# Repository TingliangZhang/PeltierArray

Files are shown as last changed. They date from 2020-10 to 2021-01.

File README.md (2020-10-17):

# PeltierArray
帕尔贴阵列 PCB and design

## 选型

MCU: Mega 2560 PRO (Embed) CH340G/ATmega2560-16AU

https://robotdyn.com/mega-2560-pro-embed-ch340g-atmega2560-16au.html

MOS管

[MOS(场效应管)/KIA50N03BD](https://item.szlcsc.com/458575.html)

接口

JST丨常用系列和型号选型推荐大全

https://www.szlcsc.com/info/13106.html

> 一开始选择 **PH系列 插座 1\*4P 间距2mm 卧插** B4B-PH-SM4-TB(LF)
>

后更改方案为

帕尔贴接口为PH2.0x2

PH-2A 2P 脚距2.0mm 直插

https://item.szlcsc.com/2693.html

温度传感器接口保持原来的

XH插座 1*2P 直针 间距2.5mm

https://item.szlcsc.com/169360.html

电源接口

> DC头：**DC连接器 DC-002-2.0A-1.3 DC插座 W11.4XD5.0XH7.4,内芯1.3,2A 12V**
>
> https://item.szlcsc.com/353351.html
>
> 可能要稍稍掰弯

更改为[AC/DC电源插座/DC-005 5.5-2.0MM 铁材质](https://item.szlcsc.com/16896.html)

发光二极管

LED灯绿_Iv=112-285_λd=520-535 二极管_发光二极管

SMT

或手贴

翠绿LED

https://item.szlcsc.com/207066.html

电容

[贴片电容/47uF(476) ±20% 25V](https://item.szlcsc.com/389810.html)

[引线型铝电解电容/47uF 50V黑高频](https://item.szlcsc.com/46672.html)

[贴片电容/10uF(106) ±20% 25V](https://item.szlcsc.com/97651.html)

其他

[肖特基二极管/SS14](https://item.szlcsc.com/2857.html)

[发光二极管/翠绿LED](https://item.szlcsc.com/207066.html)

半桥驱动

参考 [**wavgat**](https://wavgat.tmall.com/) 的MOS管驱动模块

https://detail.tmall.com/item.htm?id=599634712152

他上面用的MOS是[AOD4184A](https://item.szlcsc.com/100337.html)，N沟道

暂定选用[KIA50N03BD](https://item.szlcsc.com/458575.html)

封装为TO-252-2

## 3D MODEL

`.3dshapes`文件夹里面放`.step`和 `.wrl`模型文件，再在PCBNEW里面的元件封装属性里面选3D Setting添加3D Model，调整偏移对齐即可。

## Duplicate PCB sch and layout

参考

https://forum.kicad.info/t/how-to-duplicate-a-pcb-layout-in-kicad-5/12909

https://forum.kicad.info/t/replicate-layout-action-plugin/8539

https://github.com/MitjaNemec/Kicad_action_plugins

前提Hierarchical schematics：

https://docs.kicad-pcb.org/5.1/en/eeschema/eeschema.html#hierarchical-schematics

## 改为正反均要后需要用全桥

A5988:四路 DMOS 全桥式 PWM 电机驱动器

https://www.allegromicro.com/zh-CN/Products/Motor-Drivers/Brush-DC-Motor-Drivers/A5988

或者TB6612

https://toshiba.semicon-storage.com/us/semiconductor/product/motor-driver-ics/brushed-dc-motor-driver-ics/detail.TB6612FNG.html

或者DRV8833

https://www.ti.com/product/DRV8833

或者用以上两款电机驱动的Breakout Board，方便坏了的话更换。

或者参考Adafruit TB6612 1.2A DC/Stepper Motor Driver Breakout Board设计自己画

https://www.adafruit.com/product/2448

## 排针排母

TB6612 1x8排母

Mega Pro 2x3排母+2x16排母+2x21排母

只买2x20 2x3排母，剪一下

## TD1509配套电路

总体按照8V ~ 18V输入 5V 输出设计

SS52F肖特基二极管 20V 5A

https://item.szlcsc.com/328975.html

33uH 4.5A功率电感

https://item.szlcsc.com/160864.html

更便宜的选择：5A的33uH

https://item.szlcsc.com/338378.html

330uf/25V过孔电容

https://item.szlcsc.com/2403.html

## V2焊接过程中发现的问题

电感封装不对

TB6612引脚错误

没有开关（买个带开关的开关电源或者加一个12V回路功率开关）

指示灯，5V加LED+10k

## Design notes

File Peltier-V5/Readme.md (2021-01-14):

# 大板子设计

[PCA9685PW](https://www.nxp.com/part/PCA9685PW#/)

[AIP74HC4051](https://lcsc.com/product-detail/74-Series_Wuxi-I-core-Elec-AIP74HC4051_C93010.html)

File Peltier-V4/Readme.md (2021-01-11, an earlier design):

# 模块化帕尔贴设计

[BTN8982TA](https://www.infineon.com/cms/en/product/power/motor-control-ics/brushed-dc-motor-driver-ics/single-half-bridge-ics/btn8982ta/)

[6N137](https://toshiba.semicon-storage.com/ap-en/semiconductor/product/optoelectronics/detail.6N137.html)

[OPA2374](https://www.ti.com/product/OPA2374)

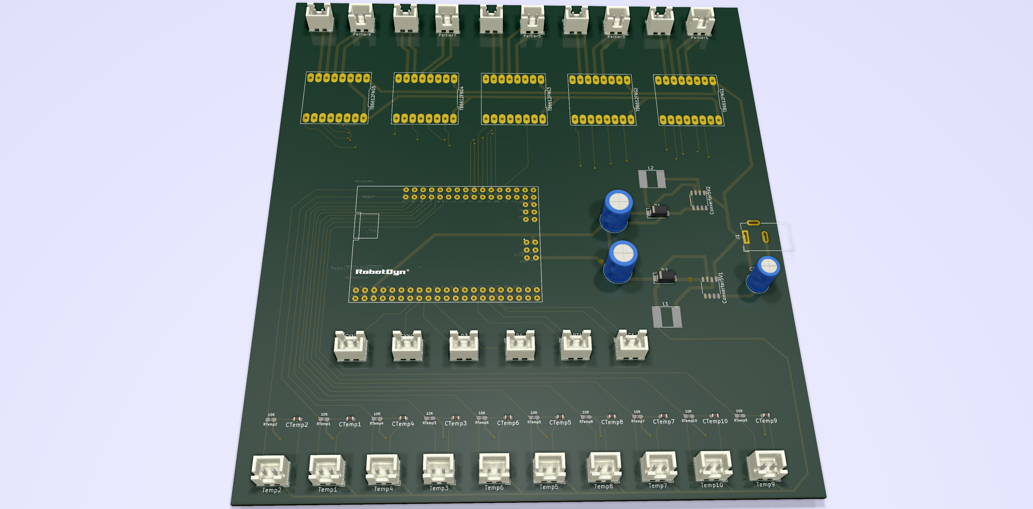
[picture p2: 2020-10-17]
Screenshot/屏幕截图 2020-10-17 140903.png

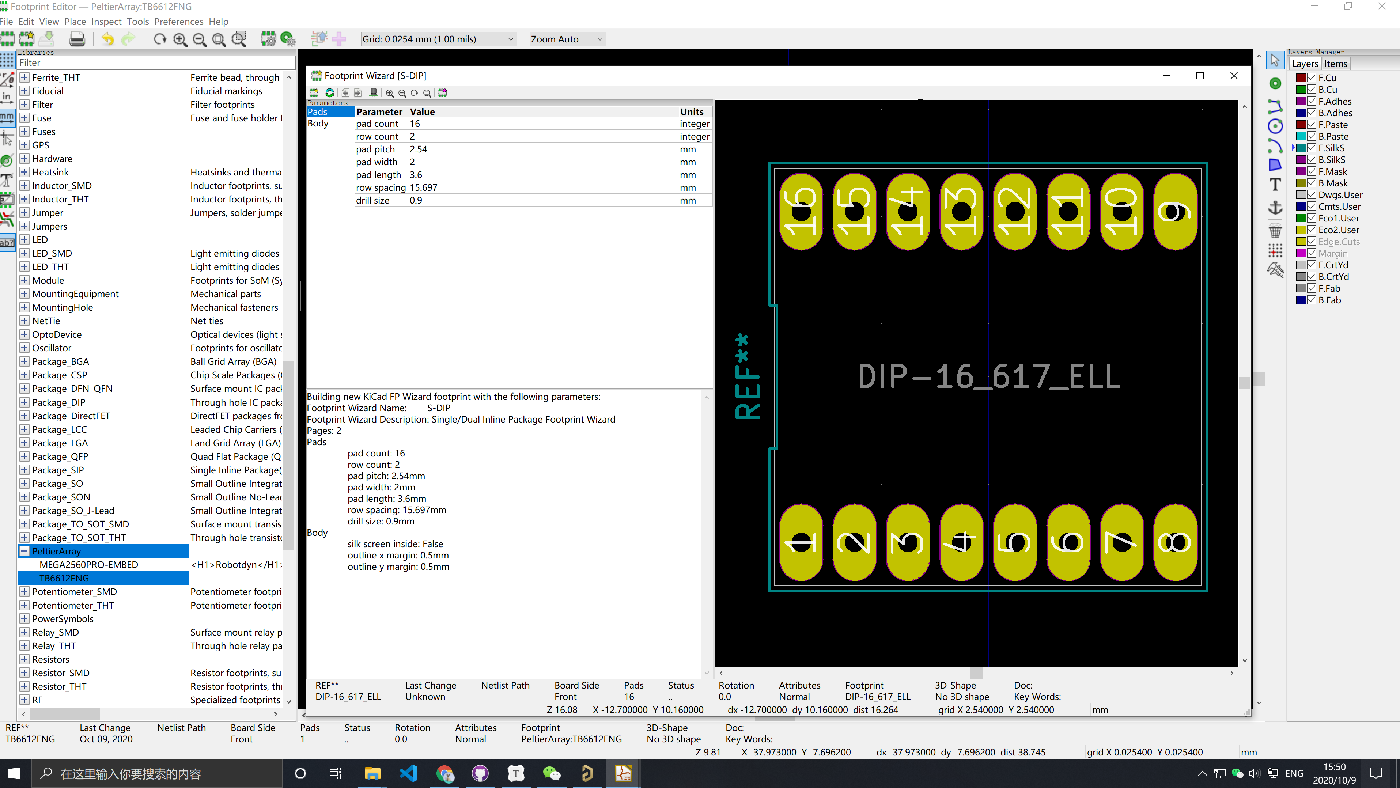
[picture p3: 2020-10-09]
Screenshot/屏幕截图 2020-10-09 155059.png

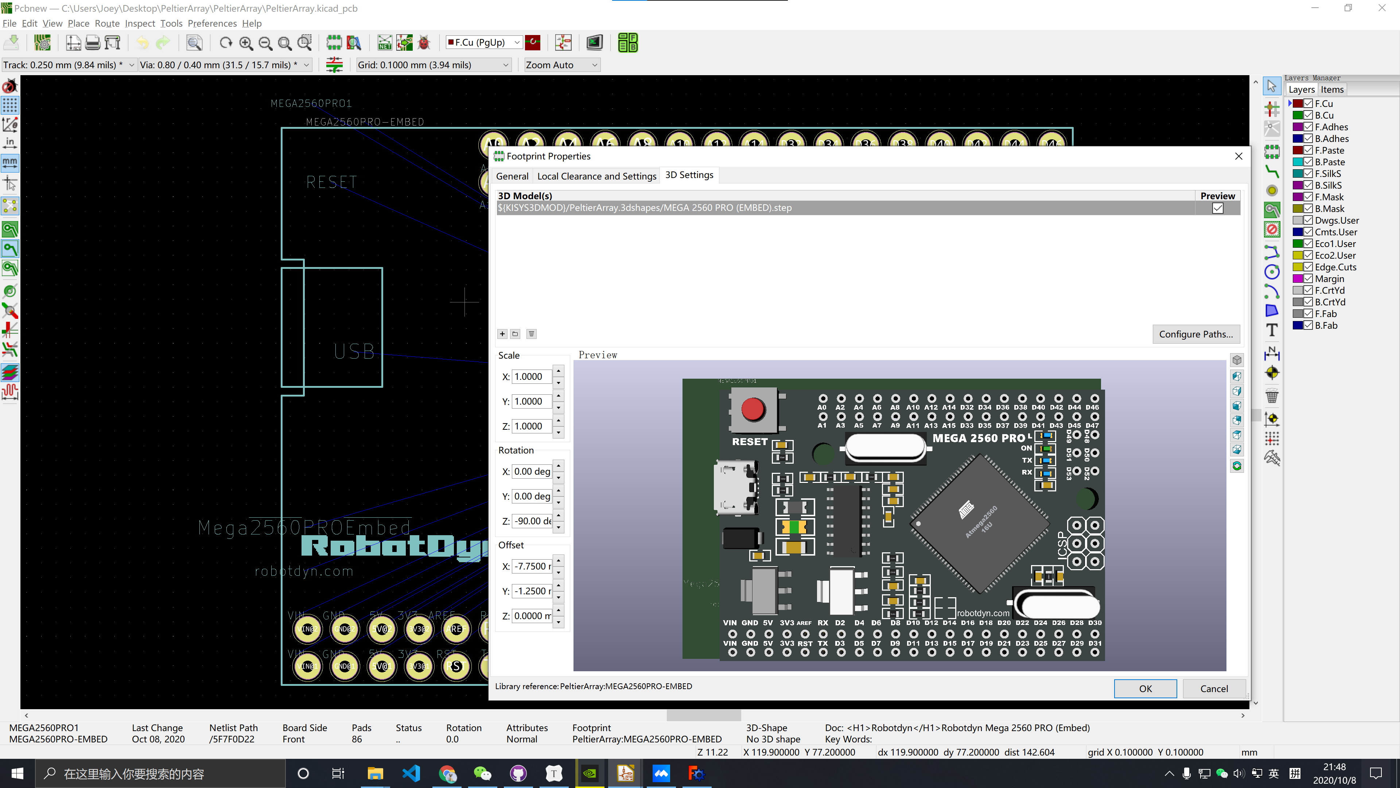
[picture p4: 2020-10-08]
ScreenShot/屏幕截图 2020-10-08 214903.png

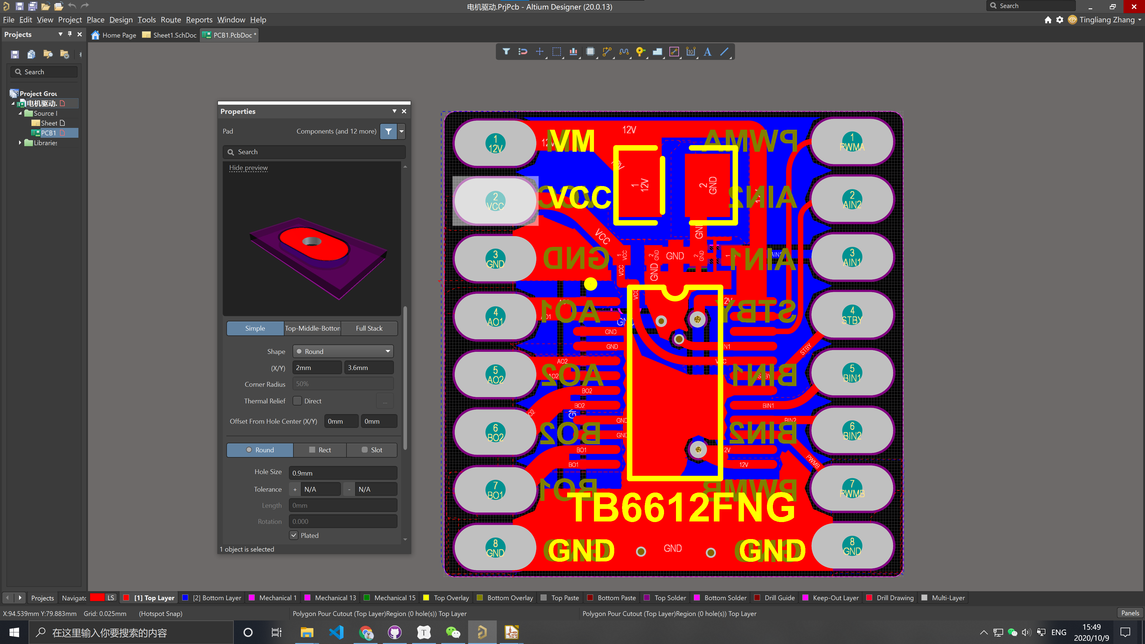
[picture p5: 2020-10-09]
Screenshot/屏幕截图 2020-10-09 154931.png

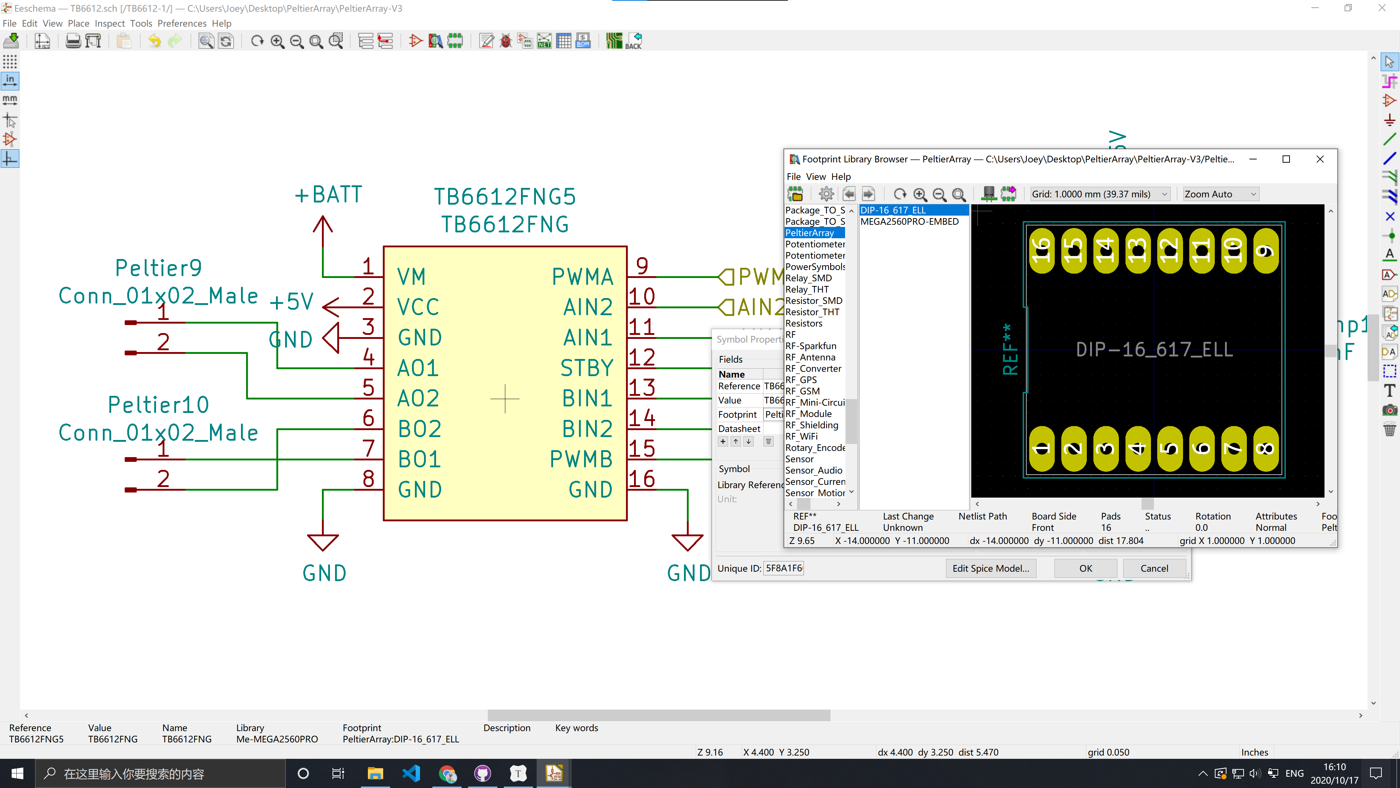
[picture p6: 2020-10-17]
Screenshot/屏幕截图 2020-10-17 161026.png

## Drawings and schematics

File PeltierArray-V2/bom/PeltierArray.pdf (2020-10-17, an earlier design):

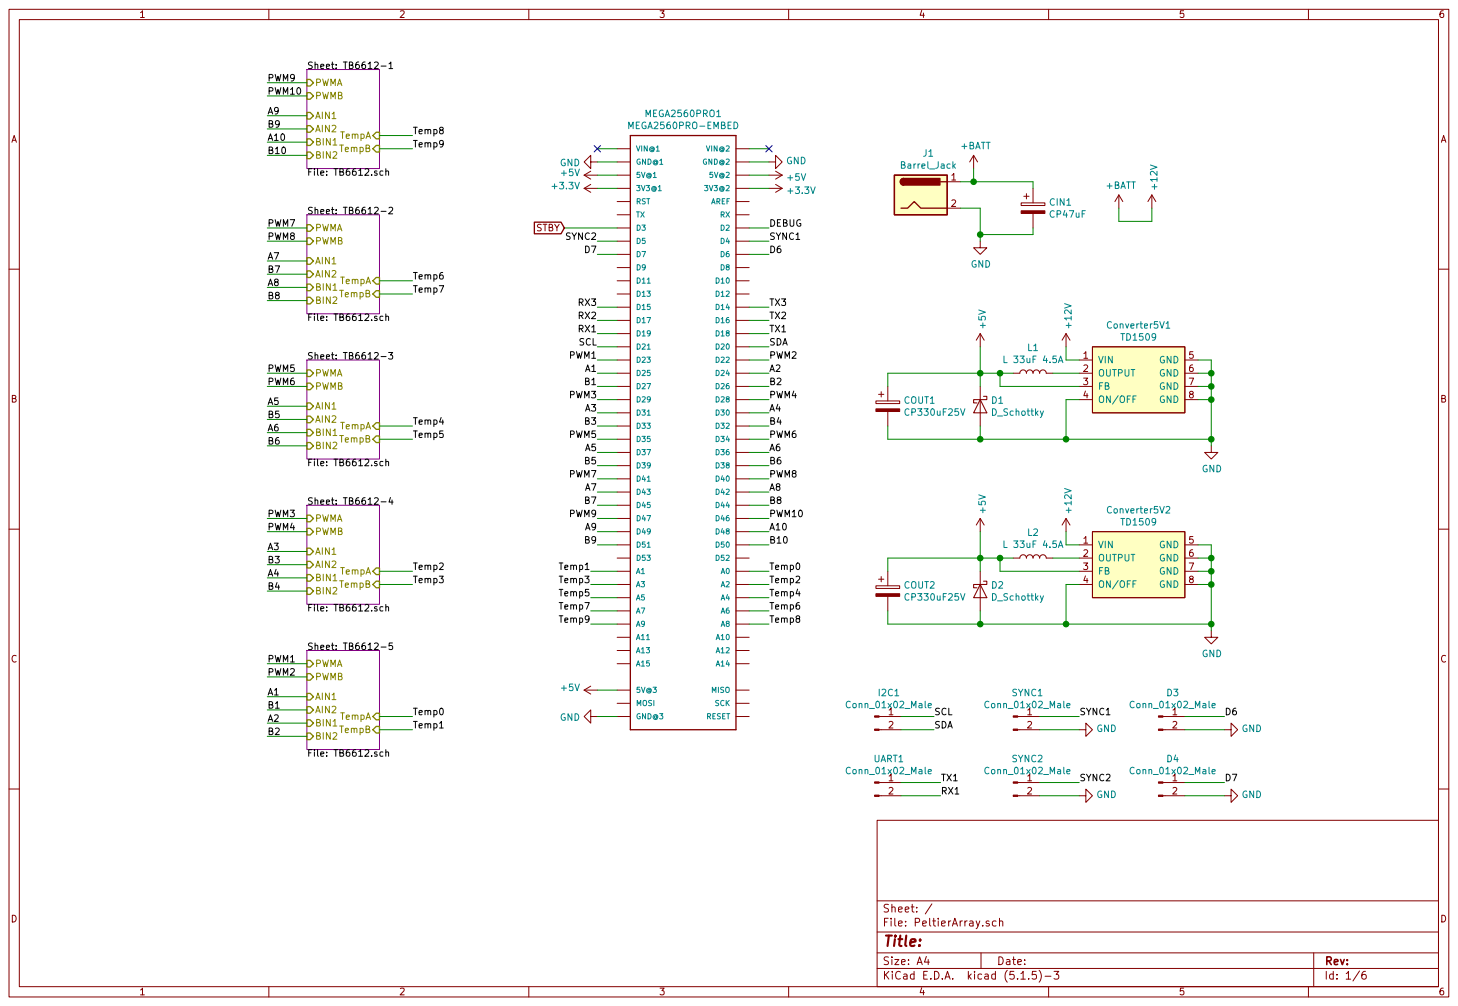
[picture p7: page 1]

Sheet: TB6612-1 File: TB6612.sch PWMA
AIN2 AIN1 BIN1 BIN2 PWMB

Sheet: TB6612-2 File: TB6612.sch PWMA

Sheet: TB6612-3 File: TB6612.sch PWMA

Sheet: TB6612-4 File: TB6612.sch PWMA

File: PeltierArray.sch Sheet: / Sheet: TB6612-5 File: TB6612.sch PWMA

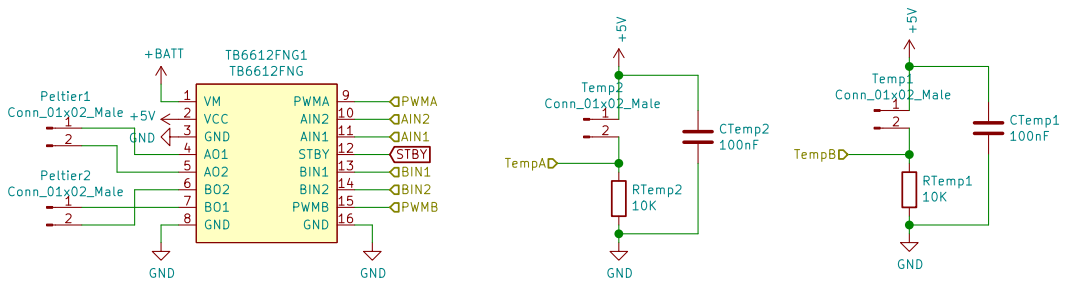
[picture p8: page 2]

Id: 2/6 Title: File: TB6612.sch Sheet: /TB6612-5/

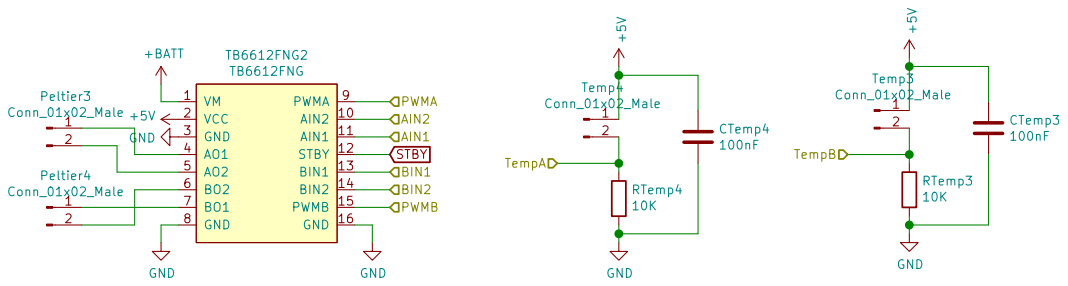
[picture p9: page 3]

Id: 3/6 Title: File: TB6612.sch Sheet: /TB6612-4/

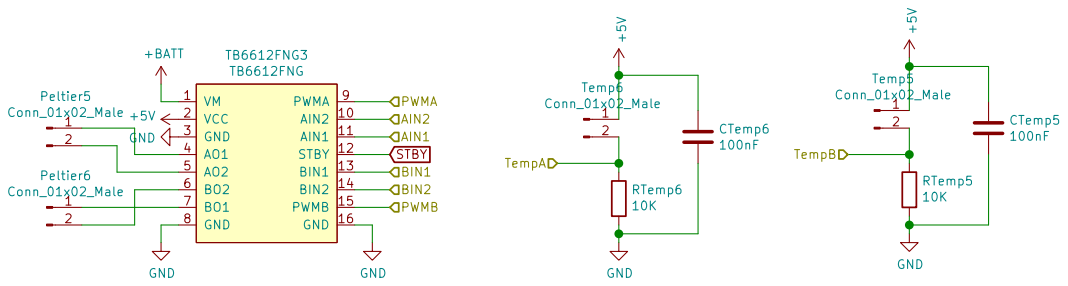
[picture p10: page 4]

Id: 4/6 Title: File: TB6612.sch Sheet: /TB6612-3/

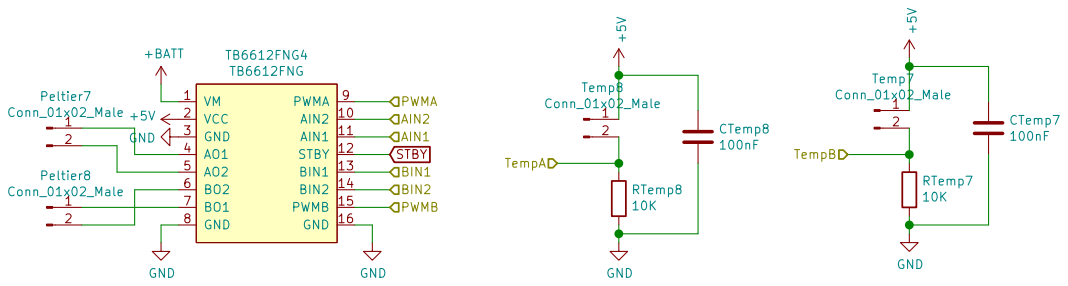
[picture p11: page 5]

Id: 5/6 Title: File: TB6612.sch Sheet: /TB6612-2/

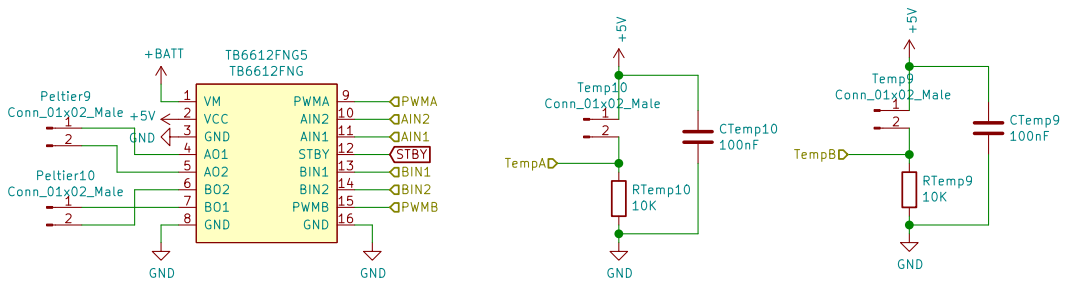
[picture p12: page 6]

Id: 6/6 Title: File: TB6612.sch Sheet: /TB6612-1/

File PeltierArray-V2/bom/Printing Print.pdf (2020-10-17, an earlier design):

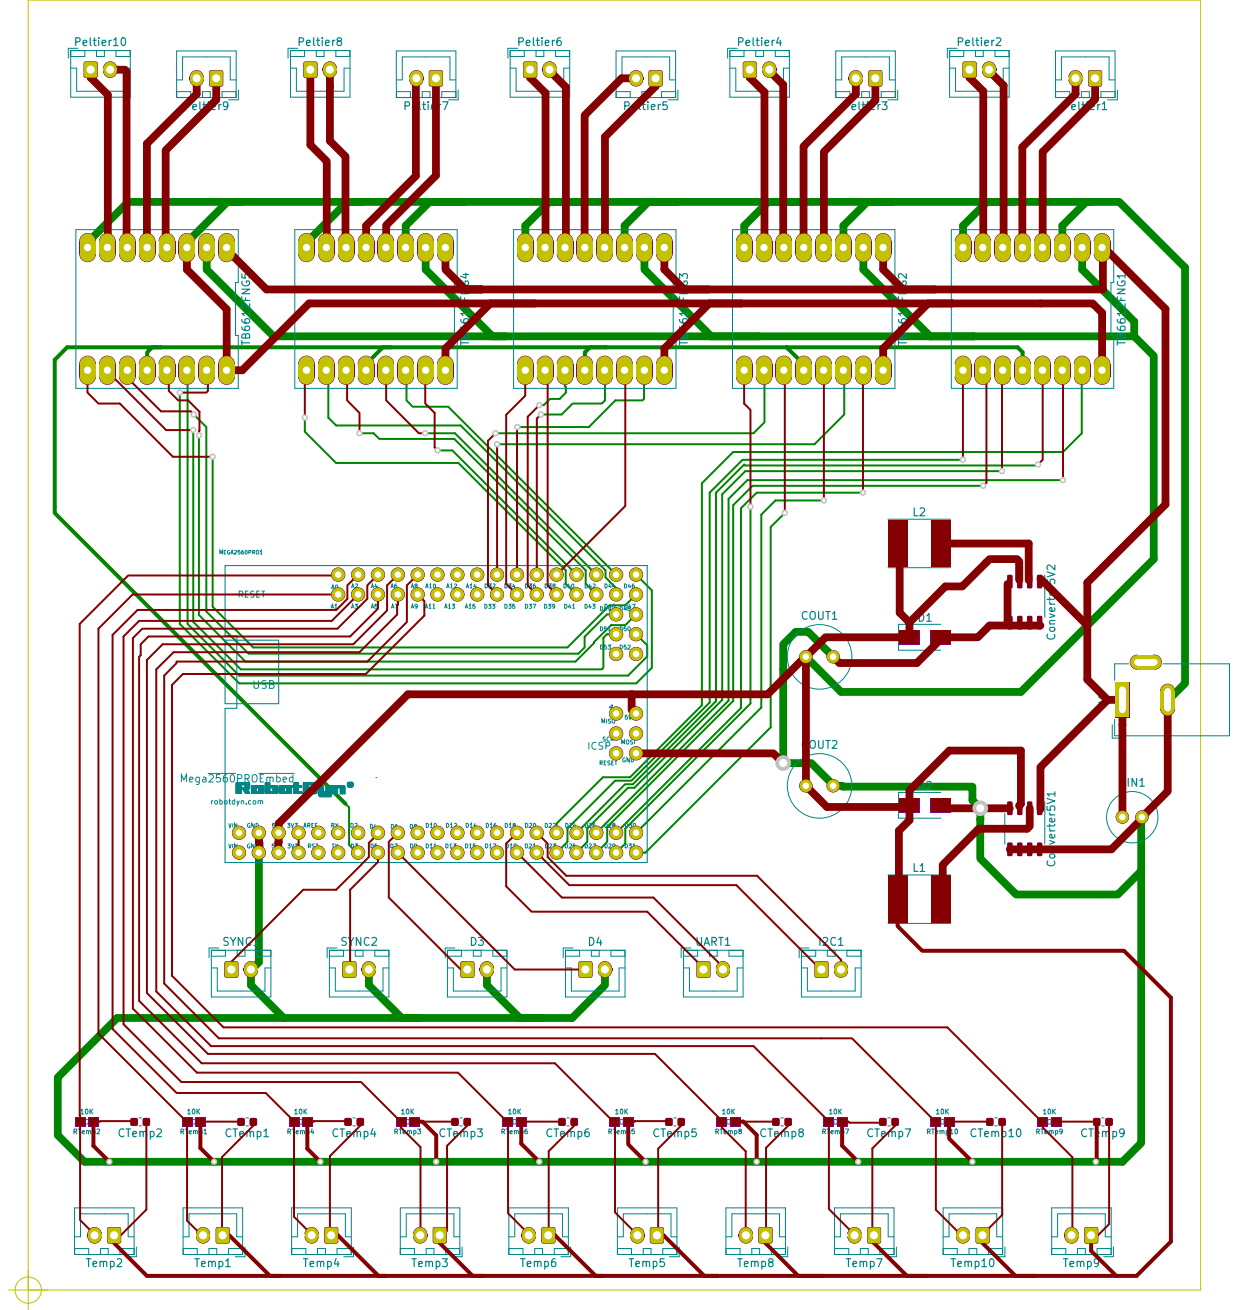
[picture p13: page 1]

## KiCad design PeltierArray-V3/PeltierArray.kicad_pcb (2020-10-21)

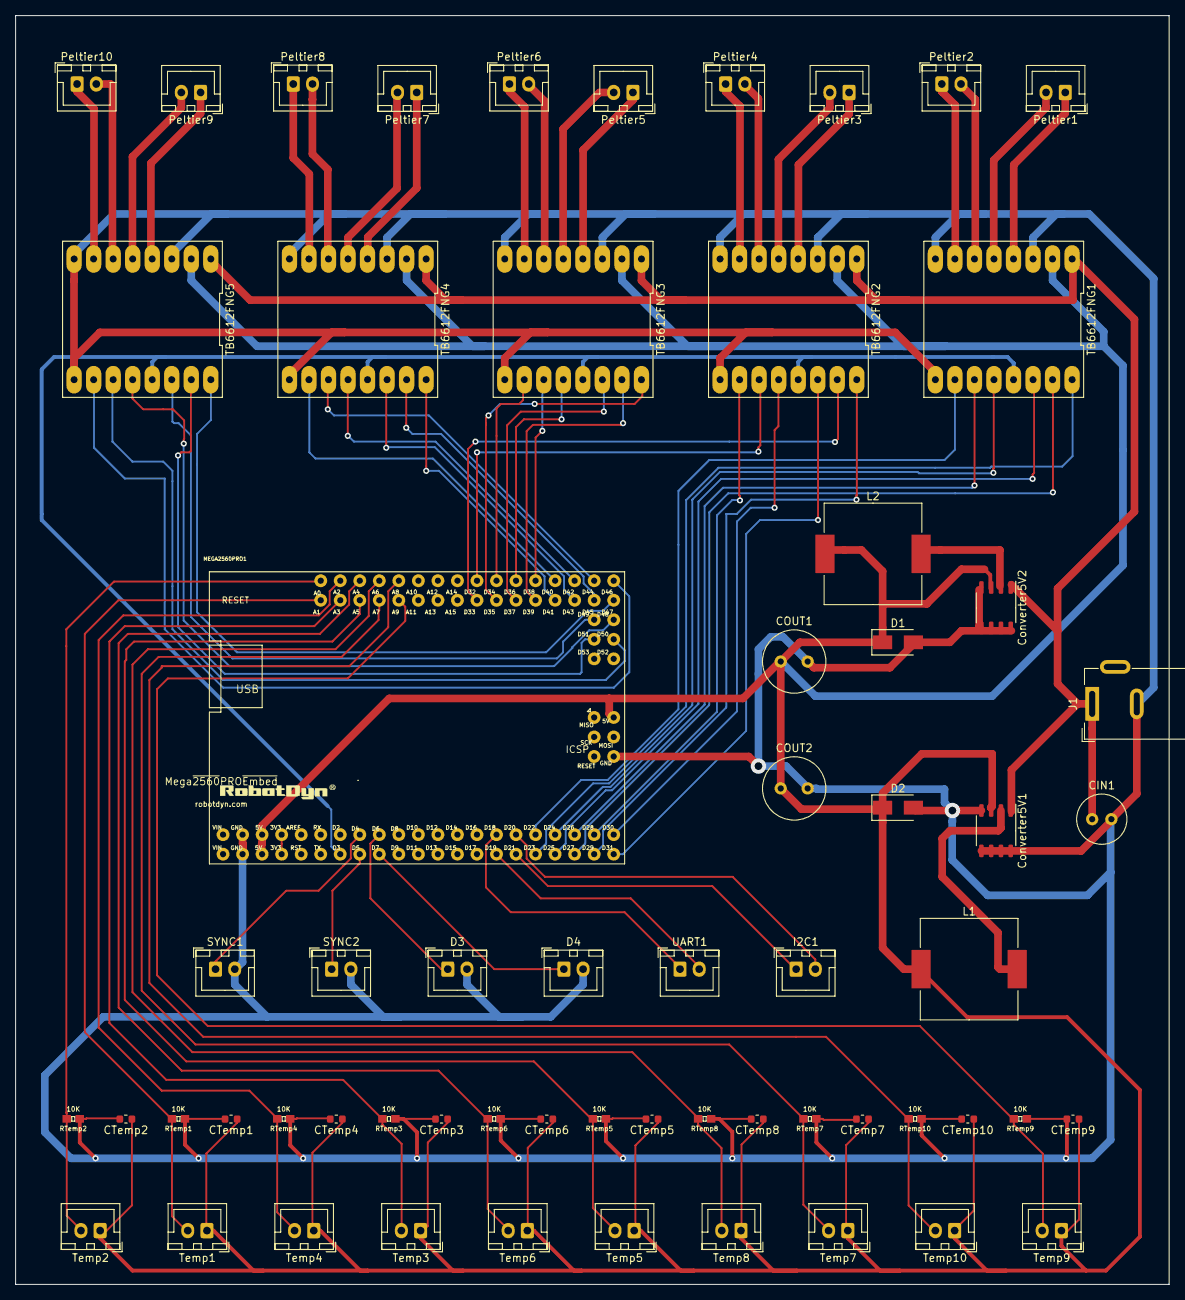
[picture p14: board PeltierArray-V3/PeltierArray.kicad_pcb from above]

Board: 2 copper layers, 150.0 x 165.0 mm, 62 parts (0 on the bottom side), 75 nets.

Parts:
CIN1: CP47uF; C_Radial_D6.3mm_H11.0mm_P2.50mm
COUT1, COUT2: CP330uF25V; C_Radial_D8.0mm_H11.5mm_P3.50mm
CTemp1, CTemp2, CTemp3, CTemp4, CTemp5, CTemp6, CTemp7, CTemp8, CTemp9, CTemp10: 100nF; C_0603_1608Metric
Converter5V1, Converter5V2: TD1509; SOP-8_3.9x4.9mm_P1.27mm
D1, D2: D_Schottky; D_SMA
D3, D4: Conn_01x02_Male; JST_XH_B2B-XH-A_1x02_P2.50mm_Vertical
I2C1: Conn_01x02_Male; JST_XH_B2B-XH-A_1x02_P2.50mm_Vertical
J1: Barrel_Jack; BarrelJack_Wuerth_6941xx301002
L1, L2: L 33uF 4.5A; L_Wuerth_HCM-1390
MEGA2560PRO1: MEGA2560PRO-EMBED
Peltier1, Peltier2, Peltier3, Peltier4, Peltier5, Peltier6, Peltier7, Peltier8, Peltier9, Peltier10: Conn_01x02_Male; JST_XH_B2B-XH-A_1x02_P2.50mm_Vertical
RTemp1, RTemp2, RTemp3, RTemp4, RTemp5, RTemp6, RTemp7, RTemp8, RTemp9, RTemp10: 10K; 0603
SYNC1, SYNC2: Conn_01x02_Male; JST_XH_B2B-XH-A_1x02_P2.50mm_Vertical
TB6612FNG1, TB6612FNG2, TB6612FNG3, TB6612FNG4, TB6612FNG5: TB6612FNG; DIP-16_617_ELL
Temp1, Temp2, Temp3, Temp4, Temp5, Temp6, Temp7, Temp8, Temp9, Temp10: Conn_01x02_Male; JST_XH_B2B-XH-A_1x02_P2.50mm_Vertical
UART1: Conn_01x02_Male; JST_XH_B2B-XH-A_1x02_P2.50mm_Vertical

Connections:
+3V3: MEGA2560PRO1.3V3@1, MEGA2560PRO1.3V3@2
+5V: COUT1.1, COUT2.1, CTemp1.1, CTemp2.1, CTemp3.1, CTemp4.1, CTemp5.1, CTemp6.1, CTemp7.1, CTemp8.1, CTemp9.1, CTemp10.1, Converter5V1.3, Converter5V2.3, D1.1, D2.1, L1.1, L2.1, MEGA2560PRO1.5V@1, MEGA2560PRO1.5V@2, MEGA2560PRO1.5V@3, TB6612FNG1.2, TB6612FNG2.2, TB6612FNG3.2, TB6612FNG4.2, TB6612FNG5.2, Temp1.1, Temp2.1, Temp3.1, Temp4.1, Temp5.1, Temp6.1, Temp7.1, Temp8.1, Temp9.1, Temp10.1
+12V: CIN1.1, Converter5V1.1, Converter5V2.1, J1.1, TB6612FNG1.1, TB6612FNG2.1, TB6612FNG3.1, TB6612FNG4.1, TB6612FNG5.1
/A1: MEGA2560PRO1.D25, TB6612FNG1.14
/A2: MEGA2560PRO1.D24, TB6612FNG1.12
/A3: MEGA2560PRO1.D31, TB6612FNG2.14
/A4: MEGA2560PRO1.D30, TB6612FNG2.12
/A5: MEGA2560PRO1.D37, TB6612FNG3.14
/A6: MEGA2560PRO1.D36, TB6612FNG3.12
/A7: MEGA2560PRO1.D43, TB6612FNG4.14
/A8: MEGA2560PRO1.D42, TB6612FNG4.12
/A9: MEGA2560PRO1.D49, TB6612FNG5.14
/A10: MEGA2560PRO1.D48, TB6612FNG5.12
/B1: MEGA2560PRO1.D27, TB6612FNG1.15
/B2: MEGA2560PRO1.D26, TB6612FNG1.11
/B3: MEGA2560PRO1.D33, TB6612FNG2.15
/B4: MEGA2560PRO1.D32, TB6612FNG2.11
/B5: MEGA2560PRO1.D39, TB6612FNG3.15
/B6: MEGA2560PRO1.D38, TB6612FNG3.11
/B7: MEGA2560PRO1.D45, TB6612FNG4.15
/B8: MEGA2560PRO1.D44, TB6612FNG4.11
/B9: MEGA2560PRO1.D51, TB6612FNG5.15
/B10: MEGA2560PRO1.D50, TB6612FNG5.11
/D6: D3.1, MEGA2560PRO1.D6
/D7: D4.1, MEGA2560PRO1.D7
/PWM1: MEGA2560PRO1.D23, TB6612FNG1.16
/PWM2: MEGA2560PRO1.D22, TB6612FNG1.10
/PWM3: MEGA2560PRO1.D29, TB6612FNG2.16
/PWM4: MEGA2560PRO1.D28, TB6612FNG2.10
/PWM5: MEGA2560PRO1.D35, TB6612FNG3.16
/PWM6: MEGA2560PRO1.D34, TB6612FNG3.10
/PWM7: MEGA2560PRO1.D41, TB6612FNG4.16
/PWM8: MEGA2560PRO1.D40, TB6612FNG4.10
/PWM9: MEGA2560PRO1.D47, TB6612FNG5.16
/PWM10: MEGA2560PRO1.D46, TB6612FNG5.10
/RX1: MEGA2560PRO1.D19, UART1.2
/SCL: I2C1.1, MEGA2560PRO1.D21
/SDA: I2C1.2, MEGA2560PRO1.D20
/SYNC1: MEGA2560PRO1.D4, SYNC1.1
/SYNC2: MEGA2560PRO1.D5, SYNC2.1
/TX1: MEGA2560PRO1.D18, UART1.1
/Temp0: MEGA2560PRO1.A0, RTemp2.2, Temp2.2
/Temp1: MEGA2560PRO1.A1, RTemp1.2, Temp1.2
/Temp2: MEGA2560PRO1.A2, RTemp4.2, Temp4.2
/Temp3: MEGA2560PRO1.A3, RTemp3.2, Temp3.2
/Temp4: MEGA2560PRO1.A4, RTemp6.2, Temp6.2
/Temp5: MEGA2560PRO1.A5, RTemp5.2, Temp5.2
/Temp6: MEGA2560PRO1.A6, RTemp8.2, Temp8.2
/Temp7: MEGA2560PRO1.A7, RTemp7.2, Temp7.2
/Temp8: MEGA2560PRO1.A8, RTemp10.2, Temp10.2
/Temp9: MEGA2560PRO1.A9, RTemp9.2, Temp9.2
GND: CIN1.2, COUT1.2, COUT2.2, CTemp1.2, CTemp2.2, CTemp3.2, CTemp4.2, CTemp5.2, CTemp6.2, CTemp7.2, CTemp8.2, CTemp9.2, CTemp10.2, Converter5V1.4, Converter5V1.5, Converter5V1.6, Converter5V1.7, Converter5V1.8, Converter5V2.4, Converter5V2.5, Converter5V2.6, Converter5V2.7, Converter5V2.8, D1.2, D2.2, D3.2, D4.2, J1.2, MEGA2560PRO1.GND@1, MEGA2560PRO1.GND@2, MEGA2560PRO1.GND@3, RTemp1.1, RTemp2.1, RTemp3.1, RTemp4.1, RTemp5.1, RTemp6.1, RTemp7.1, RTemp8.1, RTemp9.1, RTemp10.1, SYNC1.2, SYNC2.2, TB6612FNG1.3, TB6612FNG1.8, TB6612FNG1.9, TB6612FNG2.3, TB6612FNG2.8, TB6612FNG2.9, TB6612FNG3.3, TB6612FNG3.8, TB6612FNG3.9, TB6612FNG4.3, TB6612FNG4.8, TB6612FNG4.9, TB6612FNG5.3, TB6612FNG5.8, TB6612FNG5.9
unnamed: Converter5V1.2, L1.2
unnamed: Converter5V2.2, L2.2
unnamed: Peltier1.1, TB6612FNG1.4
unnamed: Peltier1.2, TB6612FNG1.5
unnamed: Peltier2.1, TB6612FNG1.7
unnamed: Peltier2.2, TB6612FNG1.6
unnamed: Peltier3.1, TB6612FNG2.4
unnamed: Peltier3.2, TB6612FNG2.5
unnamed: Peltier4.1, TB6612FNG2.7
unnamed: Peltier4.2, TB6612FNG2.6
unnamed: Peltier5.1, TB6612FNG3.4
unnamed: Peltier5.2, TB6612FNG3.5
unnamed: Peltier6.1, TB6612FNG3.7
unnamed: Peltier6.2, TB6612FNG3.6
unnamed: Peltier7.1, TB6612FNG4.4
unnamed: Peltier7.2, TB6612FNG4.5
unnamed: Peltier8.1, TB6612FNG4.7
unnamed: Peltier8.2, TB6612FNG4.6
unnamed: Peltier9.1, TB6612FNG5.4
unnamed: Peltier9.2, TB6612FNG5.5
unnamed: Peltier10.1, TB6612FNG5.7
unnamed: Peltier10.2, TB6612FNG5.6
STBY: MEGA2560PRO1.D3, TB6612FNG1.13, TB6612FNG2.13, TB6612FNG3.13, TB6612FNG4.13, TB6612FNG5.13

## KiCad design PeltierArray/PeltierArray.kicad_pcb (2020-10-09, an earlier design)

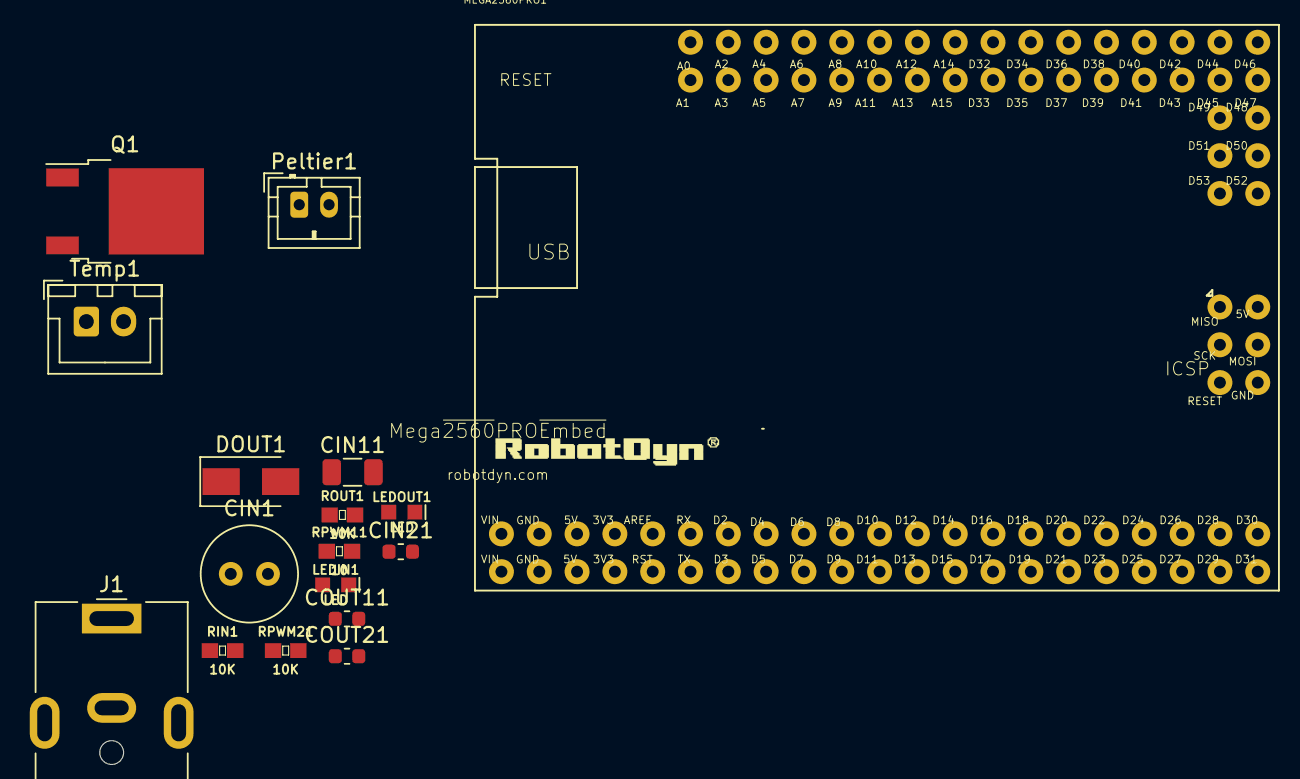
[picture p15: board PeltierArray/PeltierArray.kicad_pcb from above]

Board: 2 copper layers, 17 parts (0 on the bottom side), 8 nets, no tracks yet.

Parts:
CIN1: CP47uF; C_Radial_D6.3mm_H11.0mm_P2.50mm
CIN11: 47uF; C_1206_3216Metric
CIN21: 1uF; C_0603_1608Metric
COUT11: 10uF; C_0603_1608Metric
COUT21: 1uF; C_0603_1608Metric
DOUT1: D; D_SMA
J1: Barrel_Jack; BarrelJack_CUI_PJ-063AH_Horizontal
LEDIN1: LED; LED-0603
LEDOUT1: LED; LED-0603
MEGA2560PRO1: MEGA2560PRO-EMBED
Peltier1: Conn_01x02_Male; JST_PH_B2B-PH-K_1x02_P2.00mm_Vertical
Q1: Q_NMOS_GDS; TO-252-2
RIN1: 10K; 0603
ROUT1: 10K; 0603
RPWM11: 10; 0603
RPWM21: 10K; 0603
Temp1: Conn_01x02_Male; JST_XH_B2B-XH-A_1x02_P2.50mm_Vertical

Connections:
+3V3: MEGA2560PRO1.3V3@1, MEGA2560PRO1.3V3@2
+5V: MEGA2560PRO1.5V@1, MEGA2560PRO1.5V@2, MEGA2560PRO1.5V@3
+12V: MEGA2560PRO1.VIN@1, MEGA2560PRO1.VIN@2
+BATT: CIN1.1, CIN11.1, CIN21.1, COUT11.1, COUT21.1, DOUT1.1, J1.1, Peltier1.1, RIN1.1, ROUT1.1
/PWM1: MEGA2560PRO1.D2, RPWM11.2, RPWM21.2
GND: CIN1.2, CIN11.2, CIN21.2, J1.2, J1.MP, MEGA2560PRO1.GND@1, MEGA2560PRO1.GND@2, MEGA2560PRO1.GND@3, Q1.3, RPWM21.1, Temp1.2
unnamed: COUT11.2, COUT21.2, DOUT1.2, Peltier1.2, Q1.2
unnamed: Q1.1, RPWM11.1

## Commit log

2020-10-09 玉巨的MOS
    [PeltierArray.kicad_pcb, PeltierArray.sch]
2020-10-09 玉巨溜了
    [PeltierArray.kicad_pcb, PeltierArray.sch]
2020-10-09 Add Filter Temp Sensor
    [PeltierArray.sch]
2020-10-09 热敏电阻
    [PeltierArray.sch]
2020-10-10 Hierarchical schematics
    [PeltierArray.kicad_pcb, PeltierArray.sch, TB6612BreakoutBoard.sch]
2020-10-11 UART I2C
    [PeltierArray.kicad_pcb, PeltierArray.sch, TB6612.sch]
2021-01-13 add lib
    [PeltierCore.PcbDoc, PeltierCore.SchDoc]
